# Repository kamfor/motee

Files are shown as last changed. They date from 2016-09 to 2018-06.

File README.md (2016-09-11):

# motee_v3
Highly integrated actuator for robotics

### Components
* Pololu micro DC HP motor
* Magnetic encoder
* STM32  MCU
* TI high current H bridge
* RS485 controller 
* Logic Level converter 
* Current sensor

### Features
* Multi Master communication
* Easy commands
* Expansibility
* Arduino, Rbpi, AVR, ARM, PIC, PC compatibility 
* Task controlled
* High torque 
* ...

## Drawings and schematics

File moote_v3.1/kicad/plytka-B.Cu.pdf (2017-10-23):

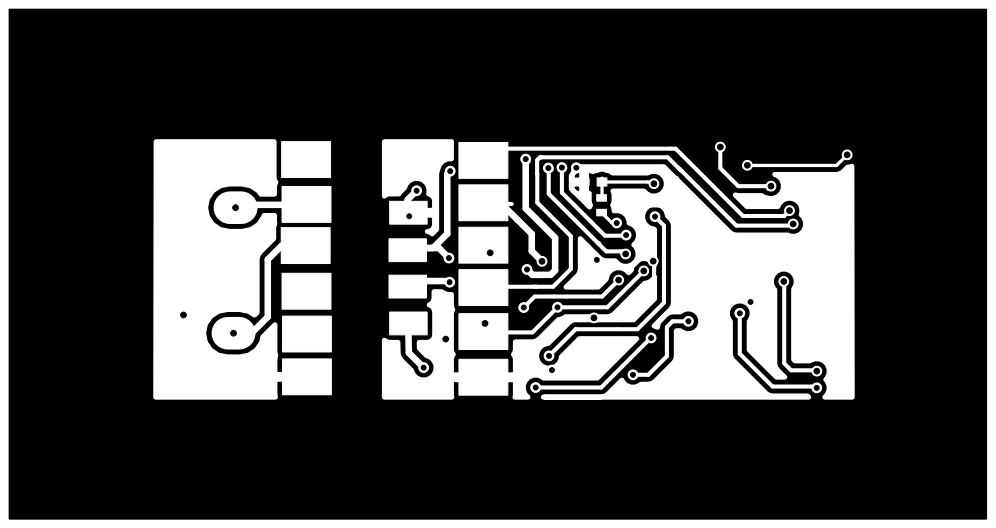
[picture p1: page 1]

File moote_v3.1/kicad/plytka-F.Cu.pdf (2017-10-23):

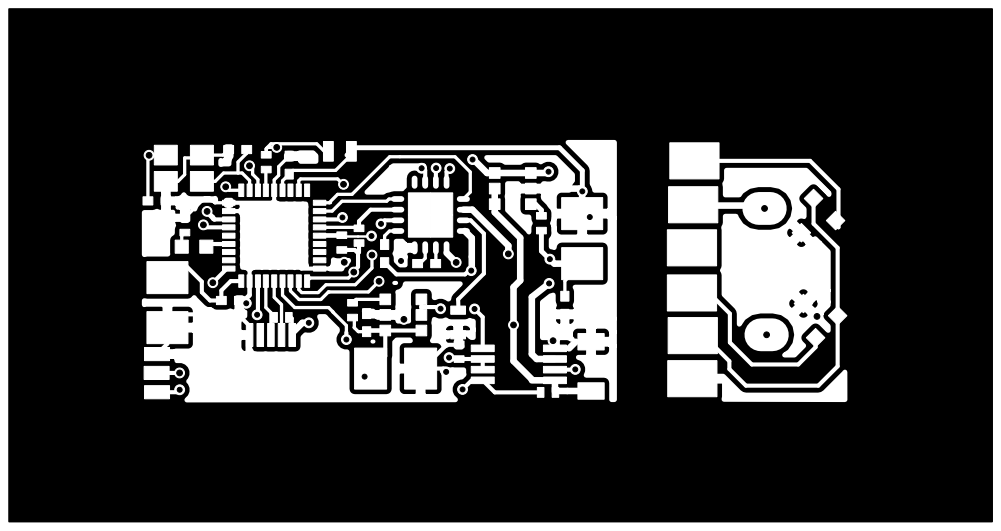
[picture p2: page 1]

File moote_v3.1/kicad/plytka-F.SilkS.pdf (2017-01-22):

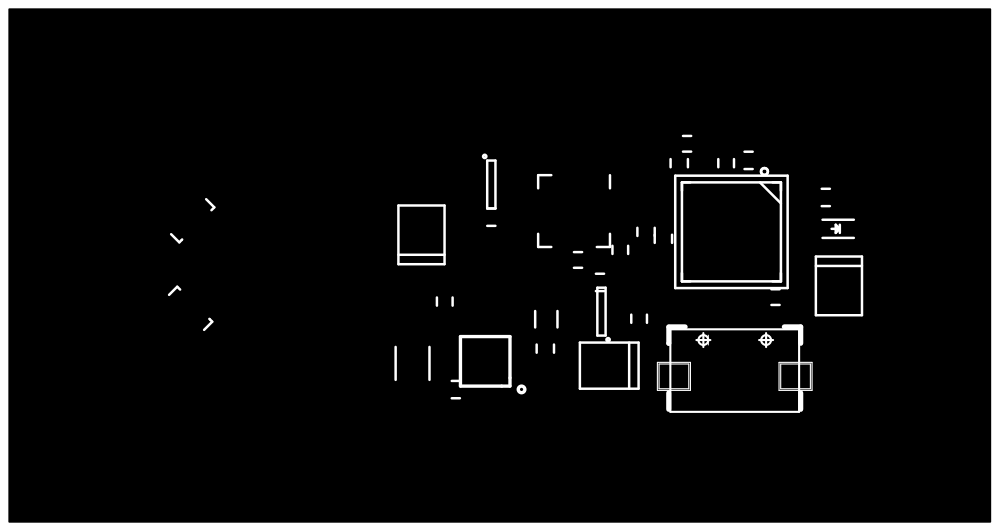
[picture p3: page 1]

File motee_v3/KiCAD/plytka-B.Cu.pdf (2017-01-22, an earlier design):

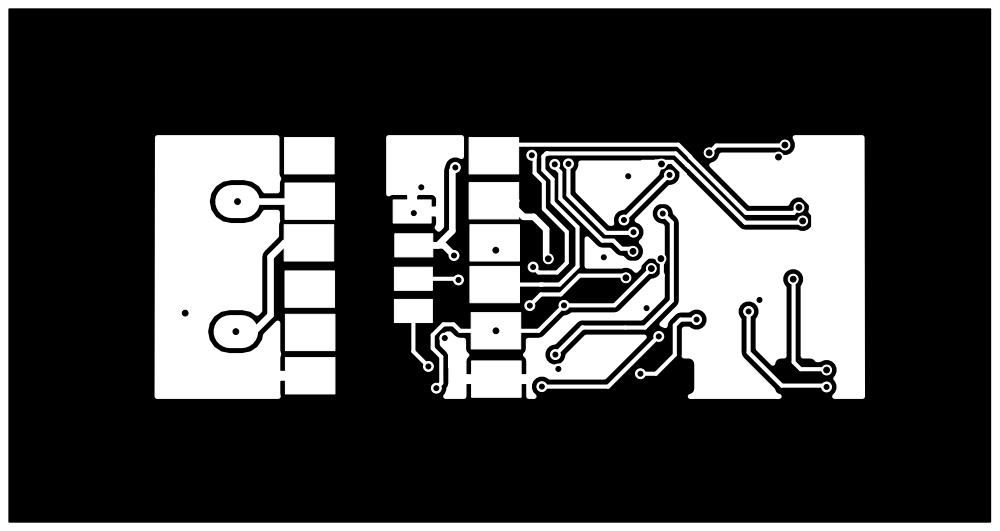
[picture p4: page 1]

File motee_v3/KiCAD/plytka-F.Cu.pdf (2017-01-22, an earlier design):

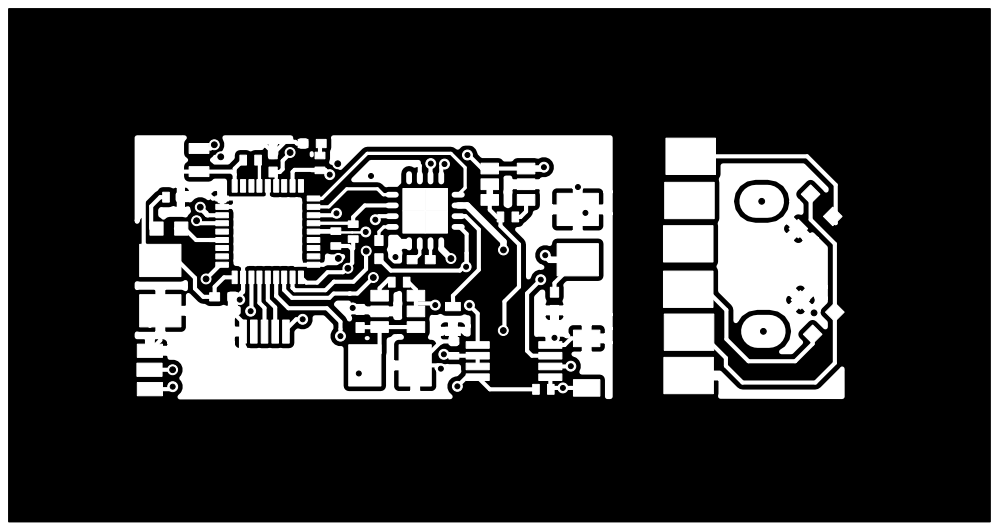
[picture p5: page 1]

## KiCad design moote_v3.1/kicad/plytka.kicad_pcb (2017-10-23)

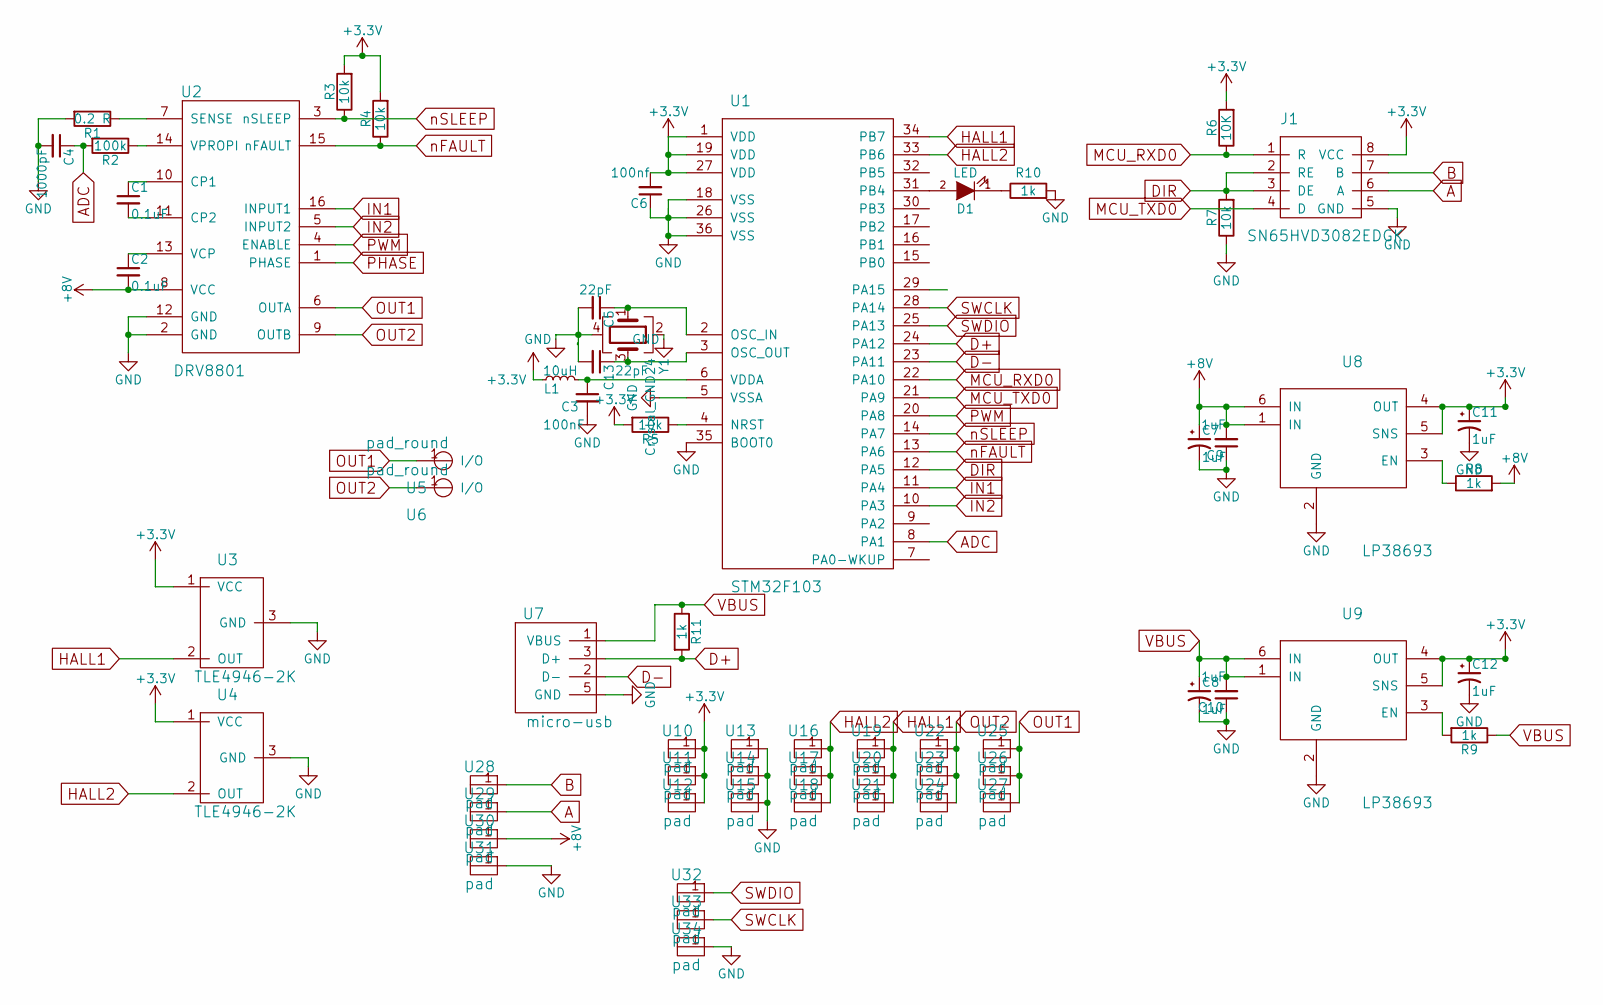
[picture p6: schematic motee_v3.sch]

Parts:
C1, C2: 0.1uF; C_0402
C3: 100nF; C_0402
C4: 1000pF; C_0402
C5, C13: 22pF; C_0402
C6: 100nf; C_0402
C7, C8, C11: 1uF; TantalC_SizeT_EIA-3528
C9, C10: 1uF; C_0402
C12: 1uF; C_1206
D1: LED; LED_0603
J1: SN65HVD3082EDGK; VSSOP8_P0.65mm_W3mm
L1: 10uH; Neosid_Inductor_SM0603CG
R1: 0.2 R; R_0603
R2: 100k; R_0402
R3, R4, R5, R7: 10k; R_0402
R6: 10K; R_0402
R8, R9, R10, R11: 1k; R_0402
U1: STM32F103; untitled-QFN50P600X600X100-37N
U2: DRV8801; UQFN-16-1EP_4x4mm_Pitch0.65mm
U3, U4: TLE4946-2K; SOT-23
U5, U6: pad_round
U7: micro-usb; microusb-USB-MICRO-SMD
U8, U9: LP38693; SOT-23-6
U10, U11, U12, U13, U14, U15, U16, U17, U18, U19, U20, U21, U22, U23, U24, U25, U26, U27: pad; pad_square
U28, U29, U30, U31: pad; pad_zlacze
U32, U33, U34: pad; pad_isp
Y1: Crystal_GND24; Crystal_SMD_SeikoEpson_FA238-4pin_3.2x2.5mm

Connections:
+3V3: C6.2, C11.1, C12.1, J1.8 (VCC), L1.1, R3.2, R4.2, R5.2, R6.2, U1.1 (VDD), U1.19 (VDD), U1.27 (VDD), U3.1 (VCC), U4.1 (VCC), U8.4 (OUT), U8.5 (SNS), U9.4 (OUT), U9.5 (SNS), U10.1, U11.1, U12.1
+8V: C2.2, C7.1, C9.2, R8.2, U2.8 (VCC), U8.1 (IN), U8.6 (IN), U30.1
A: J1.6 (A), U29.1
ADC: C4.1, R2.2, U1.8 (PA1)
B: J1.7 (B), U28.1
D+: R11.2, U1.24 (PA12), U7.3 (D+)
D-: U1.23 (PA11), U7.2 (D-)
DIR: J1.2 (RE), J1.3 (DE), R7.2, U1.12 (PA5)
GND: C3.2, C4.2, C5.2, C6.1, C7.2, C8.2, C9.1, C10.1, C11.2, C12.2, C13.2, J1.5 (GND), R1.2, R7.1, R10.2, U1.5 (VSSA), U1.18 (VSS), U1.26 (VSS), U1.35 (BOOT0), U1.36 (VSS), U2.2 (GND), U2.12 (GND), U3.3 (GND), U4.3 (GND), U7.5 (GND), U8.2 (GND), U9.2 (GND), U13.1, U14.1, U15.1, U31.1, U34.1, Y1.2, Y1.4
HALL1: U1.34 (PB7), U3.2 (OUT), U19.1, U20.1, U21.1
HALL2: U1.33 (PB6), U4.2 (OUT), U16.1, U17.1, U18.1
IN1: U1.11 (PA4), U2.16 (INPUT1)
IN2: U1.10 (PA3), U2.5 (INPUT2)
MCU_RXD0: J1.1 (R), R6.1, U1.22 (PA10)
MCU_TXD0: J1.4 (D), U1.21 (PA9)
unnamed: C1.1, U2.10 (CP1)
unnamed: C1.2, U2.11 (CP2)
unnamed: C2.1, U2.13 (VCP)
unnamed: C3.1, L1.2, U1.6 (VDDA)
unnamed: C5.1, U1.2 (OSC_IN), Y1.1
unnamed: C13.1, U1.3 (OSC_OUT), Y1.3
unnamed: D1.1 (K), R10.1
unnamed: D1.2 (A), U1.31 (PB4)
unnamed: R1.1, U2.7 (SENSE)
unnamed: R2.1, U2.14 (VPROPI)
unnamed: R5.1, U1.4 (NRST)
unnamed: R8.1, U8.3 (EN)
unnamed: R9.2, U9.3 (EN)
OUT1: U2.6 (OUTA), U5.1, U25.1, U26.1, U27.1
OUT2: U2.9 (OUTB), U6.1, U22.1, U23.1, U24.1
PWM: U1.20 (PA8), U2.4 (ENABLE)
SWCLK: U1.28 (PA14), U33.1
SWDIO: U1.25 (PA13), U32.1
VBUS: C8.1, C10.2, R9.1, R11.1, U7.1 (VBUS), U9.1 (IN), U9.6 (IN)
nFAULT: R4.1, U1.13 (PA6), U2.15 (nFAULT)
nSLEEP: R3.1, U1.14 (PA7), U2.3 (nSLEEP)

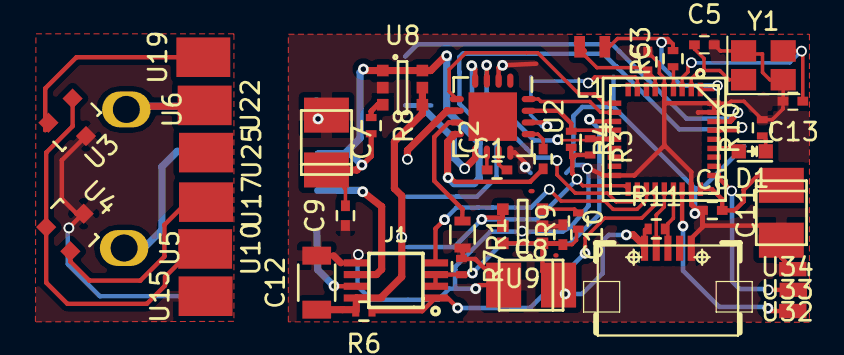
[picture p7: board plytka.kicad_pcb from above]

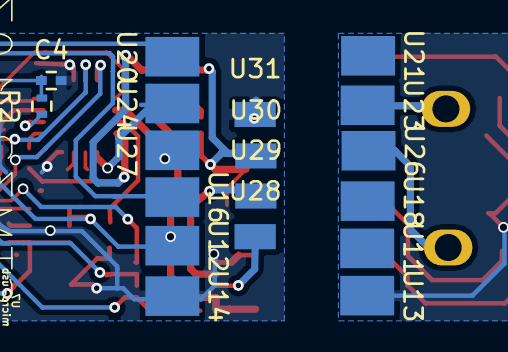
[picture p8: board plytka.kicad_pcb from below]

Board: 2 copper layers, 62 parts (18 on the bottom side), 36 nets.

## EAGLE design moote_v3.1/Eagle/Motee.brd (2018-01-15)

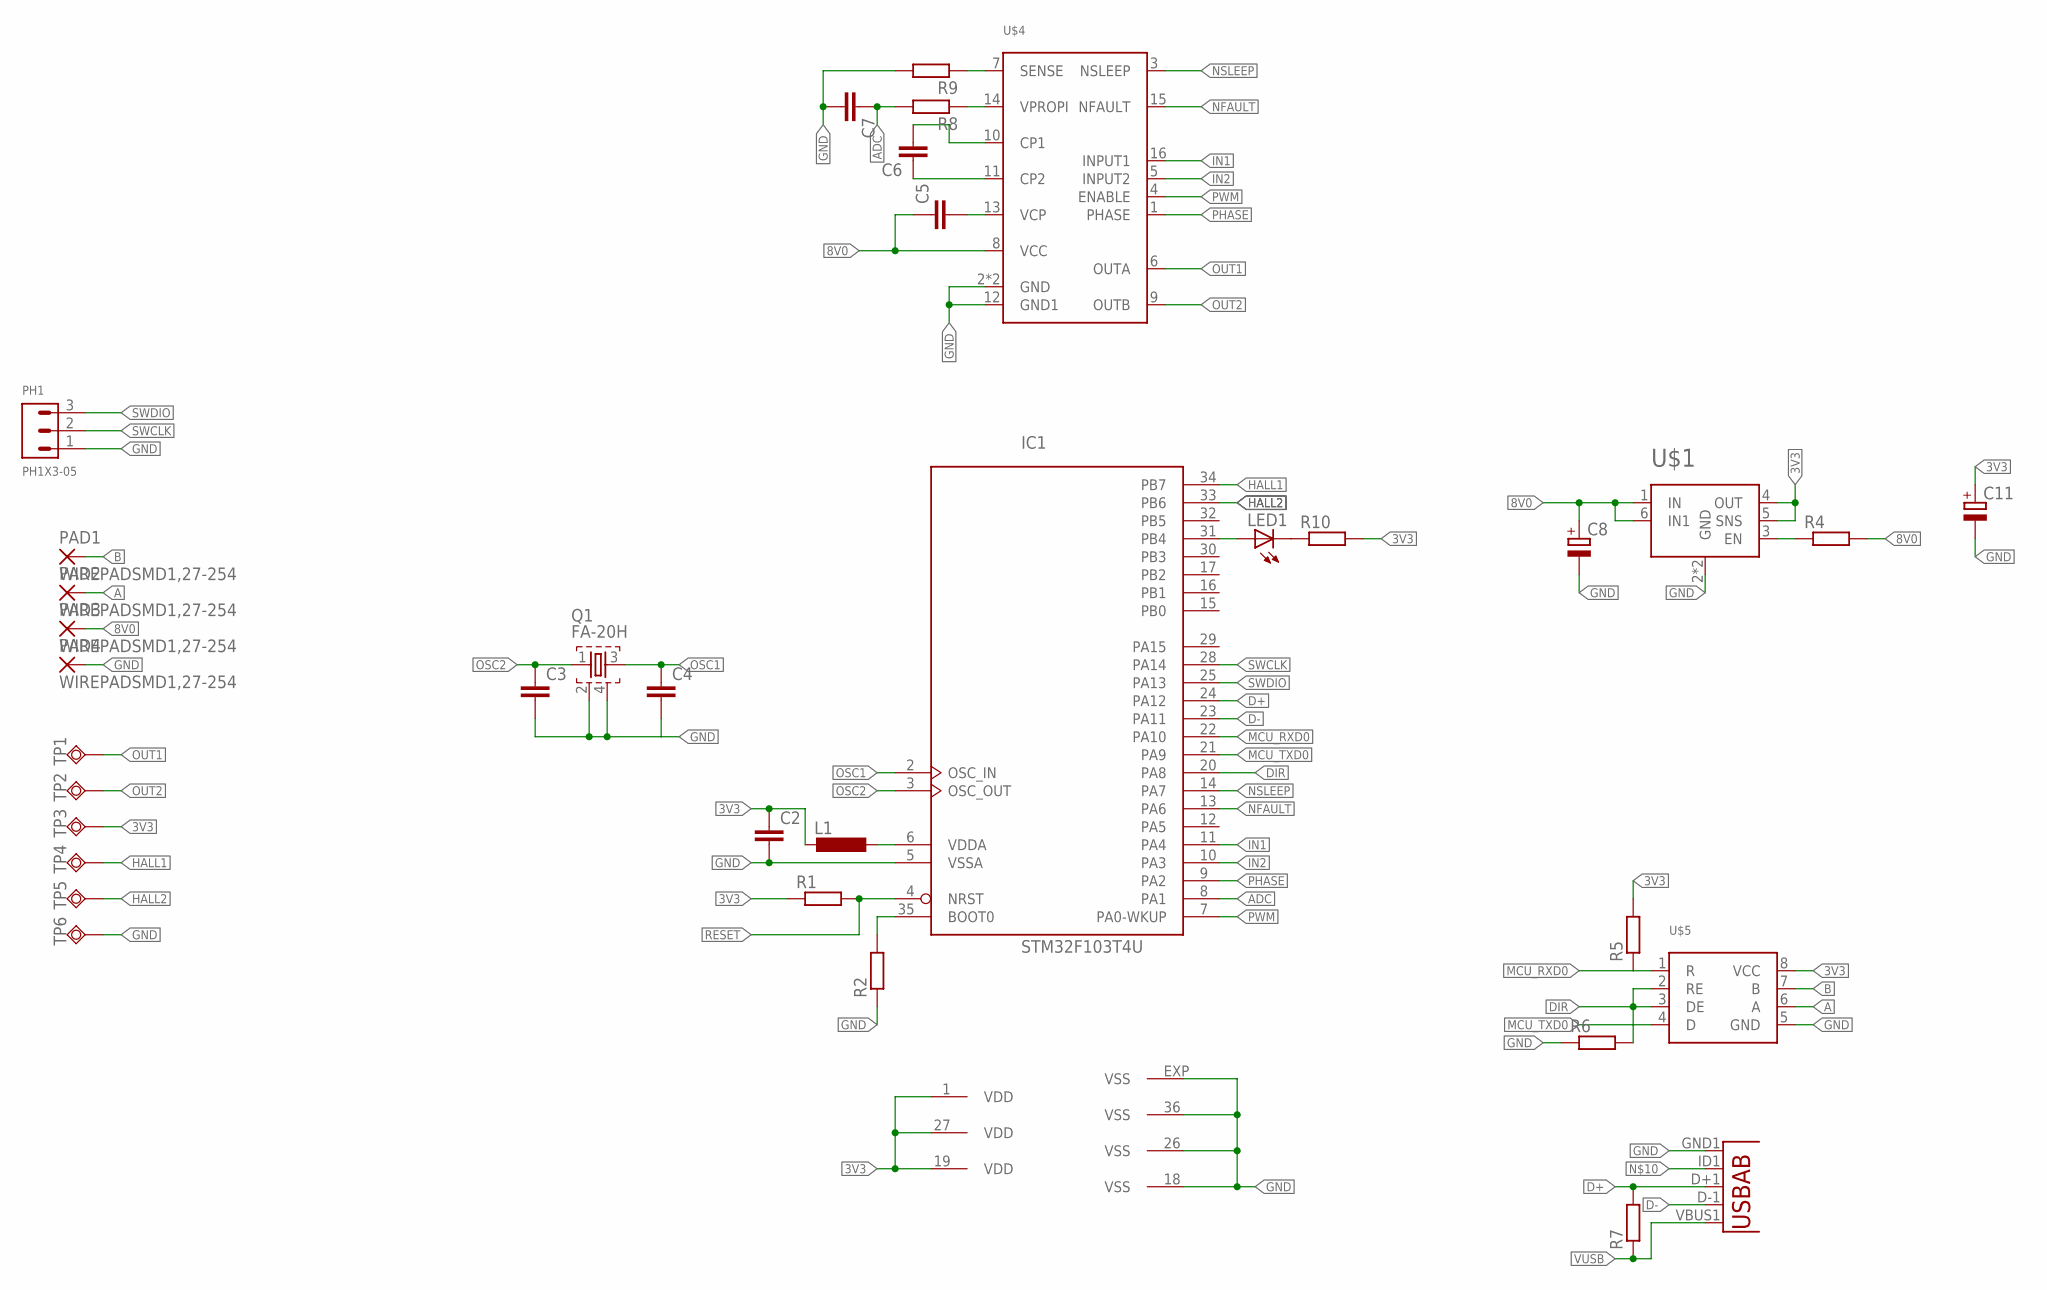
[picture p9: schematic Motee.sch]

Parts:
C2, C3, C4, C5, C6, C7: C-EUC0402K; C0402K
C8, C11: CPOL-EUB/3528-21R; B/3528-21R
IC1: STM32F103T4U; VFQFPN36
L1: L-EUL2012C; L2012C
LED1: LEDCHIP-LED0603; CHIP-LED0603
PAD1, PAD2, PAD3, PAD4: WIREPADSMD1,27-254; SMD1,27-2,54
PH1: PH1X3-05; PH005-1-3
Q1: FA-20H
R1, R2, R4, R5, R6, R7, R8, R9, R10: R-EU_R0402; R0402
TP1, TP2, TP3, TP4, TP5, TP6: TPSQTP20SQ; TP20SQ
U1: USB""; USB-MICRO-SMD
U$1: LP38693
U$4: DRV8801; WQFN-16
U$5: MAX22501EATA; TDFN-8

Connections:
3V3: C2.1, C11.+, IC1.1 (VDD), IC1.19 (VDD), IC1.27 (VDD), L1.2, R1.1, R5.2, R10.2, TP3.TP, U$1.4 (OUT), U$1.5 (SNS), U$5.8 (VCC)
8V0: C5.1, C8.+, PAD3.1, R4.2, U$1.1 (IN), U$1.6 (IN1), U$4.8 (VCC)
A: PAD2.1, U$5.6 (A)
ADC: C7.1, IC1.8 (PA1), R8.2
B: PAD1.1, U$5.7 (B)
D+: IC1.24 (PA12), R7.2, U1.D+1 (D+)
D-: IC1.23 (PA11), U1.D-1 (D-)
DIR: IC1.20 (PA8), R6.2, U$5.2 (RE), U$5.3 (DE)
GND: C2.2, C3.2, C4.2, C7.2, C8.-, C11.-, IC1.5 (VSSA), IC1.18 (VSS), IC1.26 (VSS), IC1.36 (VSS), IC1.EXP (VSS), PAD4.1, PH1.1, Q1.2, Q1.4, R2.1, R6.1, R9.2, TP6.TP, U1.GND1 (GND), U$1.2 (GND), U$1.7 (GND), U$4.2 (GND), U$4.12 (GND1), U$4.17 (GND), U$5.5 (GND)
HALL1: IC1.34 (PB7), TP4.TP
HALL2: IC1.33 (PB6), TP5.TP
IN1: IC1.11 (PA4), U$4.16 (INPUT1)
IN2: IC1.10 (PA3), U$4.5 (INPUT2)
MCU_RXD0: IC1.22 (PA10), R5.1, U$5.1 (R)
MCU_TXD0: IC1.21 (PA9), U$5.4 (D)
unnamed: IC1.35 (BOOT0), R2.2
unnamed: IC1.6 (VDDA), L1.1
unnamed: C6.1, U$4.11 (CP2)
unnamed: C5.2, U$4.13 (VCP)
unnamed: C6.2, U$4.10 (CP1)
unnamed: R4.1, U$1.3 (EN)
unnamed: R8.1, U$4.14 (VPROPI)
unnamed: R9.1, U$4.7 (SENSE)
unnamed: LED1.C, R10.1
unnamed: IC1.31 (PB4), LED1.A
NFAULT: IC1.13 (PA6), U$4.15 (NFAULT)
NSLEEP: IC1.14 (PA7), U$4.3 (NSLEEP)
OSC1: C4.1, IC1.2 (OSC_IN), Q1.3
OSC2: C3.1, IC1.3 (OSC_OUT), Q1.1
OUT1: TP1.TP, U$4.6 (OUTA)
OUT2: TP2.TP, U$4.9 (OUTB)
PHASE: IC1.9 (PA2), U$4.1 (PHASE)
PWM: IC1.7 (PA0-WKUP), U$4.4 (ENABLE)
RESET: IC1.4 (NRST), R1.2
SWCLK: IC1.28 (PA14), PH1.2
SWDIO: IC1.25 (PA13), PH1.3
VUSB: R7.1, U1.VBUS1 (VBUS)

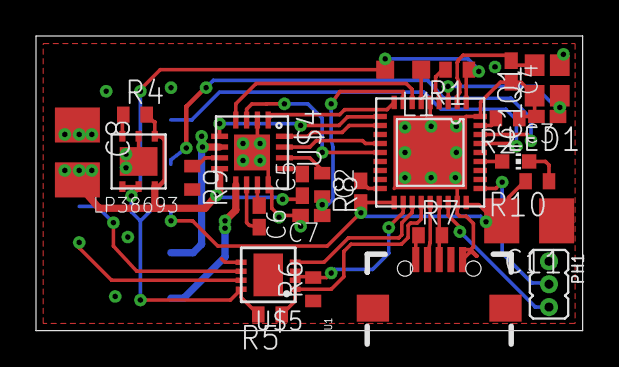
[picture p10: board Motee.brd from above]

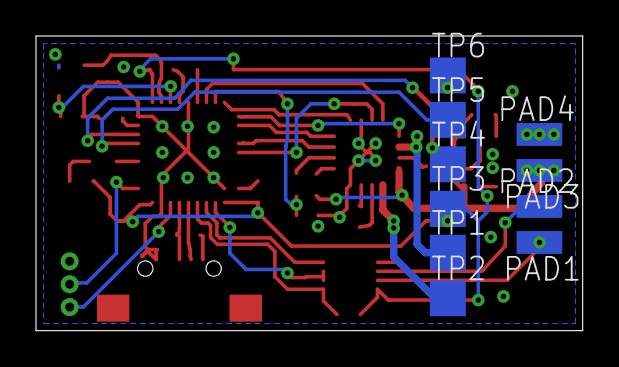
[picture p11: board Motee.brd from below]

Board: 2 copper layers, 30.4 x 16.4 mm, 36 parts (10 on the bottom side), 37 nets.

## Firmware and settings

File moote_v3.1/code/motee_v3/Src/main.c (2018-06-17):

/**
  ******************************************************************************
  * File Name          : main.c
  * Description        : Main program body
  ******************************************************************************
  */
/* Includes ------------------------------------------------------------------*/
#include "main.h"
#include "stm32f1xx_hal.h"
#include "gpio.h"

/* USER CODE BEGIN Includes */
#include "motor.h"
#include "communication.h"
/* USER CODE END Includes */


/* USER CODE BEGIN PV */

extern volatile uint8_t frameReady;

/* USER CODE END PV */

void SystemClock_Config(void);

/* USER CODE BEGIN PFP */

/* USER CODE END PFP */

int main(void)
{

  /* MCU Configuration----------------------------------------------------------*/

  /* Reset of all peripherals, Initializes the Flash interface and the Systick. */

  HAL_Init();

  /* Configure the system clock */
  SystemClock_Config();

  /* Initialize all configured peripherals */

  /* USER CODE BEGIN 2 */

  MOTOR_init();
  communication_init();

  //MOTOR_pid_test();

  /* USER CODE END 2 */

  /* Infinite loop */
  /* USER CODE BEGIN WHILE */

  while (1)
  {
  /* USER CODE END WHILE */

  /* USER CODE BEGIN 3 */
	if(frameReady==1){
		frameReady=0;
		handle_communication();
		HAL_GPIO_TogglePin(USER_LED_GPIO_Port, USER_LED_Pin);
	}
	//zHAL_GPIO_TogglePin(USER_LED_GPIO_Port, USER_LED_Pin);
	HAL_Delay(20);
	send_controls();
  }
  /* USER CODE END 3 */
}

/** System Clock Configuration
*/
void SystemClock_Config(void)
{

  RCC_OscInitTypeDef RCC_OscInitStruct;
  RCC_ClkInitTypeDef RCC_ClkInitStruct;
  RCC_PeriphCLKInitTypeDef PeriphClkInit;

    /**Initializes the CPU, AHB and APB busses clocks 
    */
  RCC_OscInitStruct.OscillatorType = RCC_OSCILLATORTYPE_HSE;
  RCC_OscInitStruct.HSEState = RCC_HSE_ON;
  RCC_OscInitStruct.HSEPredivValue = RCC_HSE_PREDIV_DIV2;
  RCC_OscInitStruct.HSIState = RCC_HSI_ON;
  RCC_OscInitStruct.PLL.PLLState = RCC_PLL_ON;
  RCC_OscInitStruct.PLL.PLLSource = RCC_PLLSOURCE_HSE;
  RCC_OscInitStruct.PLL.PLLMUL = RCC_PLL_MUL9;
  if (HAL_RCC_OscConfig(&RCC_OscInitStruct) != HAL_OK)
  {
    _Error_Handler(__FILE__, __LINE__);
  }

    /**Initializes the CPU, AHB and APB busses clocks 
    */
  RCC_ClkInitStruct.ClockType = RCC_CLOCKTYPE_HCLK|RCC_CLOCKTYPE_SYSCLK
                              |RCC_CLOCKTYPE_PCLK1|RCC_CLOCKTYPE_PCLK2;
  RCC_ClkInitStruct.SYSCLKSource = RCC_SYSCLKSOURCE_PLLCLK;
  RCC_ClkInitStruct.AHBCLKDivider = RCC_SYSCLK_DIV1;
  RCC_ClkInitStruct.APB1CLKDivider = RCC_HCLK_DIV2;
  RCC_ClkInitStruct.APB2CLKDivider = RCC_HCLK_DIV1;

  if (HAL_RCC_ClockConfig(&RCC_ClkInitStruct, FLASH_LATENCY_2) != HAL_OK)
  {
    _Error_Handler(__FILE__, __LINE__);
  }

  PeriphClkInit.PeriphClockSelection = RCC_PERIPHCLK_ADC|RCC_PERIPHCLK_USB;
  PeriphClkInit.AdcClockSelection = RCC_ADCPCLK2_DIV6;
  PeriphClkInit.UsbClockSelection = RCC_USBCLKSOURCE_PLL_DIV1_5;
  if (HAL_RCCEx_PeriphCLKConfig(&PeriphClkInit) != HAL_OK)
  {
    _Error_Handler(__FILE__, __LINE__);
  }

    /**Configure the Systick interrupt time 
    */
  HAL_SYSTICK_Config(HAL_RCC_GetHCLKFreq()/1000);

    /**Configure the Systick 
    */
  HAL_SYSTICK_CLKSourceConfig(SYSTICK_CLKSOURCE_HCLK);

  /* SysTick_IRQn interrupt configuration */
  HAL_NVIC_SetPriority(SysTick_IRQn, 0, 0);
}

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


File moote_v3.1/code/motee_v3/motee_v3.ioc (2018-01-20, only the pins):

Mcu.UserName=STM32F103T8Ux
PA0-WKUP.Signal=S_TIM2_CH1_ETR
PA1.GPIO_Label=MOTOR_CURRENT
PA1.Signal=ADCx_IN1
PA10.Signal=USART1_RX
PA11.Signal=USB_DM
PA12.Signal=USB_DP
PA13.Signal=SYS_JTMS-SWDIO
PA14.Signal=SYS_JTCK-SWCLK
PA2.GPIO_Label=MOTOR_PHASE
PA2.Signal=GPIO_Output
PA3.GPIO_Label=MOTOR_MODE2
PA3.Signal=GPIO_Output
PA4.GPIO_Label=MOTOR_MODE1
PA4.Signal=GPIO_Output
PA6.GPIO_Label=MOTOR_FAULT
PA6.Signal=GPIO_Input
PA7.GPIO_Label=MOTOR_SLEEP
PA7.Signal=GPIO_Output
PA8.GPIO_Label=RS485_DIR
PA8.Signal=GPIO_Output
PA9.Signal=USART1_TX
PB4.GPIO_Label=USER_LED
PB4.Signal=GPIO_Output
PB6.Signal=S_TIM4_CH1
PB7.Signal=S_TIM4_CH2
PD0-OSC_IN.Signal=RCC_OSC_IN
PD1-OSC_OUT.Signal=RCC_OSC_OUT

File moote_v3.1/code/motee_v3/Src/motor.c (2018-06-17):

/**
*@file motor.c
*@brief this file contains functions for steering dc motor and getting value from encoder
*@author Kamil Foryszewski
*/

#include "motor.h"

float setPoint;
float motorPidControl;
uint8_t setDirection;
uint8_t controlOn=0;
uint16_t procesVariable;
uint16_t speedRegister;
uint16_t maxSpeed=1000;

void MOTOR_init(void){
	 MX_GPIO_Init(); //GPIO controll
	 MX_TIM4_Init(); //encoder mode
	 MX_ADC1_Init(); //current sense
	 MX_TIM2_Init(); //PWM generation
	 MX_TIM1_Init(); //200Hz Loop for PID

	 HAL_TIM_PWM_Start(&htim2, TIM_CHANNEL_1);
	 HAL_TIM_Base_Start_IT(&htim1);
	 HAL_TIM_Encoder_Start(&htim4, TIM_CHANNEL_ALL);
	 HAL_ADC_Start(&hadc1);

	 pid_init(50.0, 2.0, 1.0);
}

void MOTOR_pid_test(){
	controlOn = 1;
	setPoint = 10;
	HAL_Delay(1000);
	HAL_Delay(1000);
	controlOn = 0;
	setPoint = 0;
}

void MOTOR_enable(){
	HAL_GPIO_WritePin(MOTOR_SLEEP_GPIO_Port, MOTOR_SLEEP_Pin, GPIO_PIN_SET);
}

void MOTOR_disable(){
	HAL_GPIO_WritePin(MOTOR_SLEEP_GPIO_Port, MOTOR_SLEEP_Pin, GPIO_PIN_RESET);
}

void MOTOR_set_dir_forward(){
	HAL_GPIO_WritePin(MOTOR_PHASE_GPIO_Port, MOTOR_PHASE_Pin, GPIO_PIN_RESET);
}
void MOTOR_set_dir_reverse(){
	HAL_GPIO_WritePin(MOTOR_PHASE_GPIO_Port, MOTOR_PHASE_Pin, GPIO_PIN_SET);
}
void MOTOR_brake_on(){
	HAL_GPIO_WritePin(MOTOR_MODE1_GPIO_Port, MOTOR_MODE1_Pin, GPIO_PIN_SET);
}
void MOTOR_brake_off(){
	HAL_GPIO_WritePin(MOTOR_MODE1_GPIO_Port, MOTOR_MODE1_Pin, GPIO_PIN_RESET);
}

void MOTOR_pid_on(){
	controlOn=1;
}

void MOTOR_pid_off(){
	controlOn=0;
}

void MOTOR_set_point(float point){
	setPoint = point;
}

float MOTOR_get_set_point(){
	return setPoint;
}

void MOTOR_set_direction(uint8_t setDir){
	setDirection = setDir;
}

void MOTOR_set_max_speed(uint16_t speed){
	maxSpeed = speed;
}


uint8_t MOTOR_get_direction(){
	return setDirection;
}

uint16_t MOTOR_get_proces_variable(){
	return procesVariable;
}

void MOTOR_set_speed(float speed){
	if (speed >= 0.0){
		MOTOR_set_dir_forward();
	}else{
		MOTOR_set_dir_reverse();
		speed = -speed;
	}
	speedRegister = (uint16_t)speed;
	if(speedRegister >maxSpeed){
		TIM2->CCR1 = maxSpeed;
	}else TIM2->CCR1 = speedRegister;
}

void MOTOR_get_encoder_value(){
	procesVariable = TIM4->CNT;
	TIM4->CNT = 0;
}

uint16_t MOTOR_get_current(){
	uint16_t read =0;
	if (HAL_ADC_PollForConversion(&hadc1, 10) == HAL_OK) {
		read = HAL_ADC_GetValue(&hadc1);
		HAL_ADC_Start(&hadc1);
	}
	return read;
}

void HAL_TIM_PeriodElapsedCallback(TIM_HandleTypeDef *htim){
	MOTOR_get_encoder_value();
	if(controlOn==1){

		if (procesVariable>10000){
			procesVariable = 65536-procesVariable;
		}
		motorPidControl = pid_calculate(setPoint, (float)procesVariable);
		if(setDirection==1){
			motorPidControl = -1.0*motorPidControl;
		}
		MOTOR_set_speed(motorPidControl);
	}
	else {
	MOTOR_set_speed(0);
	}
}

/************************ KF **********************************END OF FILE****/

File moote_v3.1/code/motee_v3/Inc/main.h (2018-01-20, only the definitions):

#define MOTOR_CURRENT_Pin GPIO_PIN_1
#define MOTOR_CURRENT_GPIO_Port GPIOA
#define MOTOR_PHASE_Pin GPIO_PIN_2
#define MOTOR_PHASE_GPIO_Port GPIOA
#define MOTOR_MODE2_Pin GPIO_PIN_3
#define MOTOR_MODE2_GPIO_Port GPIOA
#define MOTOR_MODE1_Pin GPIO_PIN_4
#define MOTOR_MODE1_GPIO_Port GPIOA
#define MOTOR_FAULT_Pin GPIO_PIN_6
#define MOTOR_FAULT_GPIO_Port GPIOA
#define MOTOR_SLEEP_Pin GPIO_PIN_7
#define MOTOR_SLEEP_GPIO_Port GPIOA
#define RS485_DIR_Pin GPIO_PIN_8
#define RS485_DIR_GPIO_Port GPIOA
#define USER_LED_Pin GPIO_PIN_4
#define USER_LED_GPIO_Port GPIOB

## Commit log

2016-09-14 rezystor i dioda 0805
    [motee_v3.sch, plytka.kicad_pcb]
2016-09-29 wylane masy i boot0
    [motee_v3.kicad_pcb, motee_v3.sch, plytka.kicad_pcb]
2017-01-22 bug fixes
    [motee_v3.sch, plytka.kicad_pcb]
2017-10-23 blinky v3.1
    [motee_v3 Run.cfg, motee_v3.sch, plytka.kicad_pcb]
2017-11-02 encoder works
2017-11-07 simple PID
2017-12-16 usart frame handling
    [serial_test Debug.cfg]
2018-01-10 battery suport
2018-01-15 rs485 works
    [Motee.brd, Motee.sch]
2018-01-16 pid loop fail
2018-01-20 Pid Works

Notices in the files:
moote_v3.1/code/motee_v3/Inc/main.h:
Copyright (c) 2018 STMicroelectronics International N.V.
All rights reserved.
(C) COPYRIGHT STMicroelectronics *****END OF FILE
